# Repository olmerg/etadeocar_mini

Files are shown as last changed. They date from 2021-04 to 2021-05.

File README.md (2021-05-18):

# Tadeo Car
## Robótica industrial
Con este proyecto se busca diseñar a escala el vehículo eléctrico proyecto ETadeo Car, realizado por la universidad de Bogotá Jorge Tadeo Lozano. Este vehículo corresponde a un modelo eléctrico con tracción de cuatro ruedas utilizando servomotores [Dynamixel](http://www.dynamixel.com). El desarrollo incluye las etapas de; diseño, construcción, prueba de motores, construcción del circuito teniendo en cuenta la posibilidad de control mediante bluetooth y programación del controlador integrando la cinemática del robot para relacionarlo con velocidad lineal y angular de entrada.

El resultado final de este proyecto se encuentra en [este enlace](https://youtu.be/BBhkFSA11gs).

## Industrial robotics 2021-1
This project seeks to scale the electric vehicle ETadeo Car project, carried out by the University of Bogotá Jorge Tadeo Lozano. This vehicle corresponds to an electric model with four-wheel drive using [Dynamixel](http://www.dynamixel.com) servo motors. Development includes the stages of; design, construction, motor testing, circuit construction taking into account the possibility of bluetooth control and controller programming integrating the kinematics of the robot to relate it to linear and angular input velocity.

The final result of this project can be found at [this link](https://youtu.be/BBhkFSA11gs).

### Construccción
Teniendo en cuenta el diseño determinado para lograr una escala aproximada en la estructura de 1:4, son empleados elementos de la marca robotis para la construcción de cada una de los grupos móviles de joint y wheel.
Como elemento chasis se tiene el uso de riel DIN, con el fin de lograr una estructura rígida, reduciendo el peso y con ventajas para el ensamble rápido y ajustes ante cambios que puedan presentarse en el diseño.  Es importante tener en cuenta el acople entre cables para lograr la extensión que permita alcanzar la distancia parámetro entre la base de las ruedas. Sin embargo, es fundamental observar la forma de entrada en los motores, ya que estos no permiten adaptabilidad a modelos que se puedan encontrar en el mercado genérico. Esto lo convierte en un recurso limitante en la construcción del modelo a escala junto con los tornillos que permiten la unión de las partes.

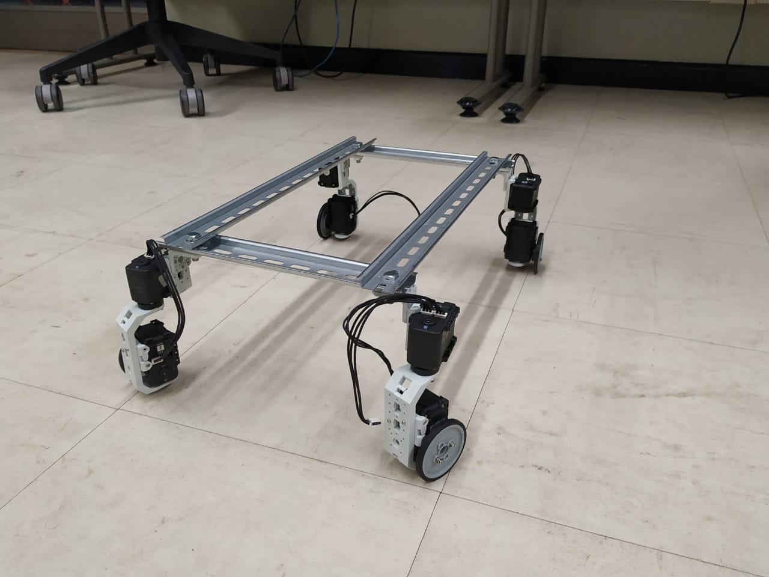
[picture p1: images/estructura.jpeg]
Estructura eTadeoCar


Antes de hacer la unión de los grupos de joint y wheel al chasis, se realizaron pruebas con los motores en el software Dynamixel Wizard 2.0 con la utilización de el hardware de robotis USB2Dynamixel, quien precisa de un controlador en el computador para su uso efectivo. En este se caracterizaron los motores según el movimiento que realizan (joint o wheel), se configuraron las ID para utilizar en la programación y los baudios de comunicación, los cuales son adaptados en 1000000.

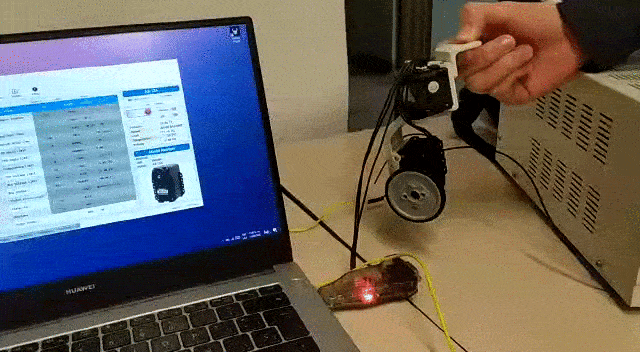
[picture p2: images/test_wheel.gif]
Dynamixel wheel

Dynamixel joint

### URDF
Se modeló el robot utilzando URDF dentro del entorno de ROS, utilizando piezas generadas en formato .stl en el programa Autodesk Inventor. Este modelo sirvio para observar la posición y los movimientos que podía tener cada joint y cada wheel.
(Las piezas pueden ser encontradas [aquí](Piezas)).

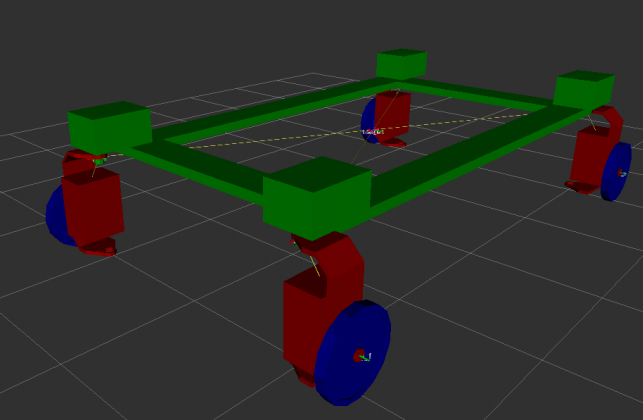
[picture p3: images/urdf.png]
urdf


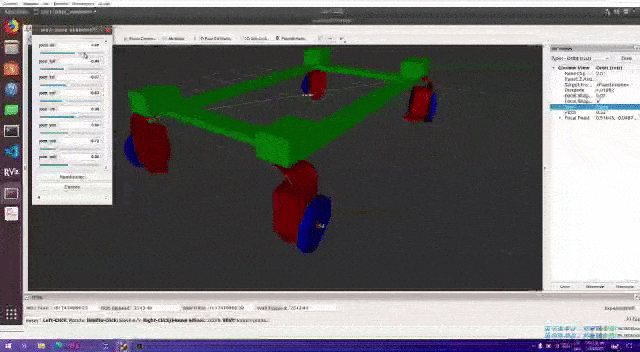
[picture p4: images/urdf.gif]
urdf


Del cual se generó la cadena cinemática

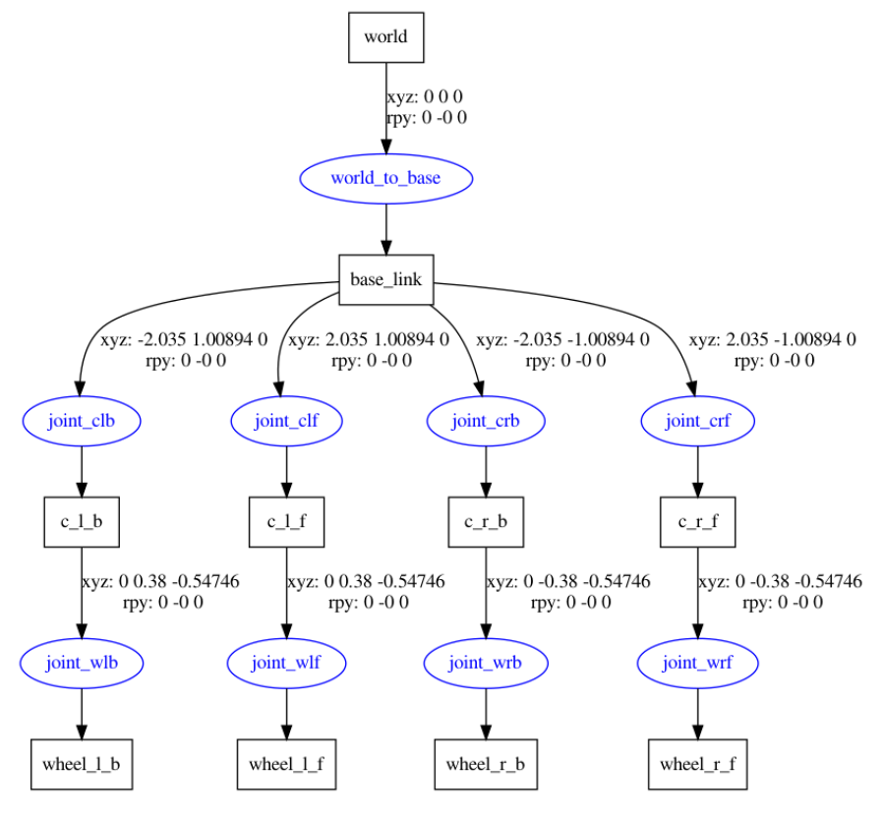
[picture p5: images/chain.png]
kinematic chain


### Circuito
Los componentes inmersos en el circuito que permite el funcionamiento del modelo son; controlador Arduino Mega 2560. Integrado SN74lS241N, el cual permite la comunicación entre el controlador y los motores al ser un buffer tri-estado. Módulo bluetooth HC-06 para el control remoto del modelo a escala. Fuente de poder que permita la alimentación de los motores dynamixel. (FotoCircuito)

El funcionamiento de este circuito puede describirse desde la potencia de entrada, para esto fue empleada la fuente que nos permite tener a la salida 12V a 5A DC, siendo adecuada para la alimentación de los motores dynamixel. Es importante destacar el negativo común para el controlador y el integrado. Adicional a esto, se debe tener en cuenta el orden de los pines para iniciar la serie que alimenta los motores 

Dynamixel pinout

La conexión del circuito integrado nos permite tener la comunicación entre el controlador Arduino Mega 2560 y los motores Dynamixel, debido a el tratamiento que este le da a los datos para permitir figurar como transmisor y receptor. En el caso descrito se utiliza el pin 2 de Arduino como pin de control y los pines 18 y 19, correspondientes a TX1 y RX1 correspondientemente. Se deben tener en cuenta conexiones propias del circuito para su funcionamiento Para el funcionamiento del módulo bluetooth realizamos la conexión de TXD del HC-06 al pin 15 de la placa Arduino correspondiente al RX3. Por su parte, el Pin RXD está conectado al pin 14 de la placa Arduino correspondiente a TX3.
El voltaje positivo de 5v para la alimentación de la placa Arduino se obtiene de la fuente brindada por el computador. La alimentación del circuito integrado y el módulo bluetooth es obtenido de la fuente del Arduino, utilizando su salida de 5v. No olvidar que es común el valor correspondiente a  0V. Se encuentra contenido en el repositorio el circuito impreso.

Las conexiones en protoboard del circuito se presentan a continuación junto con el diseño realizado en Proteus.

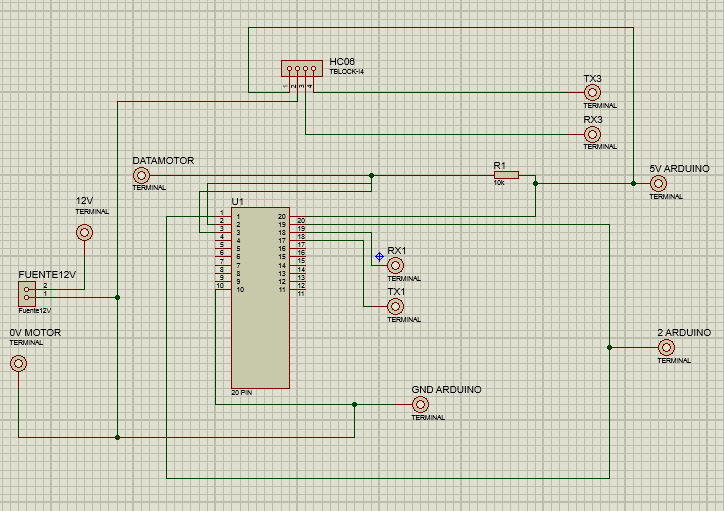
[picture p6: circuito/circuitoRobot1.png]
Proteus Circuit

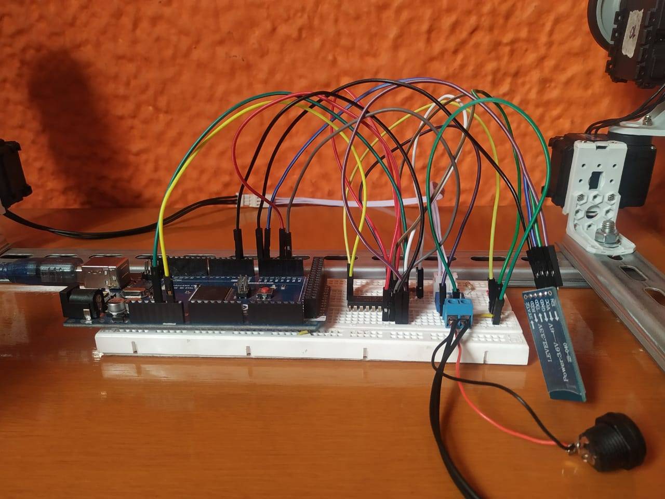
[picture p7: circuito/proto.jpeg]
Protoboard


### Código

Se programaron los servomotores utilizando [Arduino](https://www.arduino.cc) con la librería `Dynamixel.h`, las funciones creadas para desarrollar toda la lógica de funcionamiento fueron:

```
/**
 * Calcula la velocidad que debe tener cada rueda
*/
void computeVel()
```
```
/**
 * Calculan el ángulo de cada joint
*/
void computeAng()
void computeAngAux()
```
```
/**
 * Retorna el sentido de giro de la rueda
 * Toma de parámetro la velocidad
*/
int selectSide(float vel)
```
```
/**
 * Pone en movimiento cada una de las ruedas
*/
void runCar()
```
```
/**
 * Gira cada joint a la posición deseada
*/
void turn()
```
```
/**
 * Deja los joint en posiciión 0
 * Detiene todos los motores
*/
void stopAll()
```
### Conexión Bluetooth

Con el uso de la aplicación bluetooth electronics descargada en Android, se permite la realización de un panel para control del modelo. Esta aplicación se conecta de forma sencilla con el módulo para iniciar la transmisión de datos.
Como se aprecia en la imágen, se utiliza un pad de 4 posiciones para enviar el carácter deseado que se procesa en el código para su ejecución en los motores Dynamixel. También se cuenta con un botón de parada, útil en cualquier momento ante algún imprevisto que se pueda presentar durante la ejecución. 

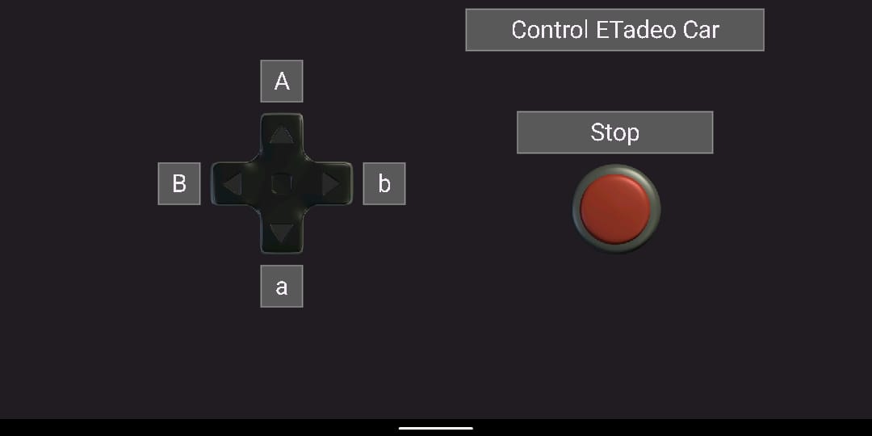
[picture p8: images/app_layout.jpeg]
Bluetooth App


En esta aplicación se emplea un pad de 4 posiciones para enviar un caracter que esta relacionado con el código en la programación, asociado respectivamente con un movimiento específico. En este caso como se aprecia en la imágen, los caracteres utilizados para el movimiento del robot son A, a, B, b. Por su parte, se emplea un botón (buttons) de color rojo, el cual está asociado al caracter s para el paro del robot y vuelta a la posición inicial. La aplicacion se encuentra en [esta ruta](App).

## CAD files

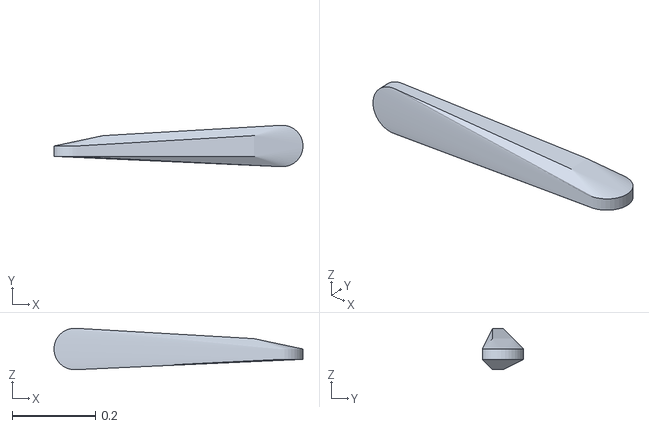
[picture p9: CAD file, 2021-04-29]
lesson_urdf/meshes/collision/arm_link_twist_2.stl
0.6 x 0.0997 x 0.0997

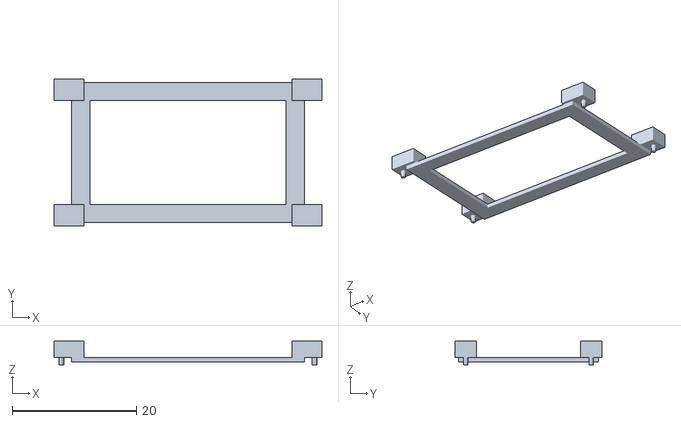
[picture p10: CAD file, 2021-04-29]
Piezas/Rieles.stl
43.1 x 23.7 x 3.80

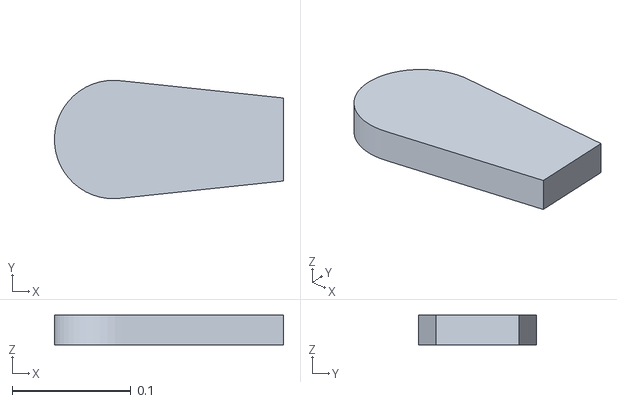
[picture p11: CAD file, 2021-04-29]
lesson_urdf/meshes/collision/gripper.stl
0.193 x 0.1 x 0.025

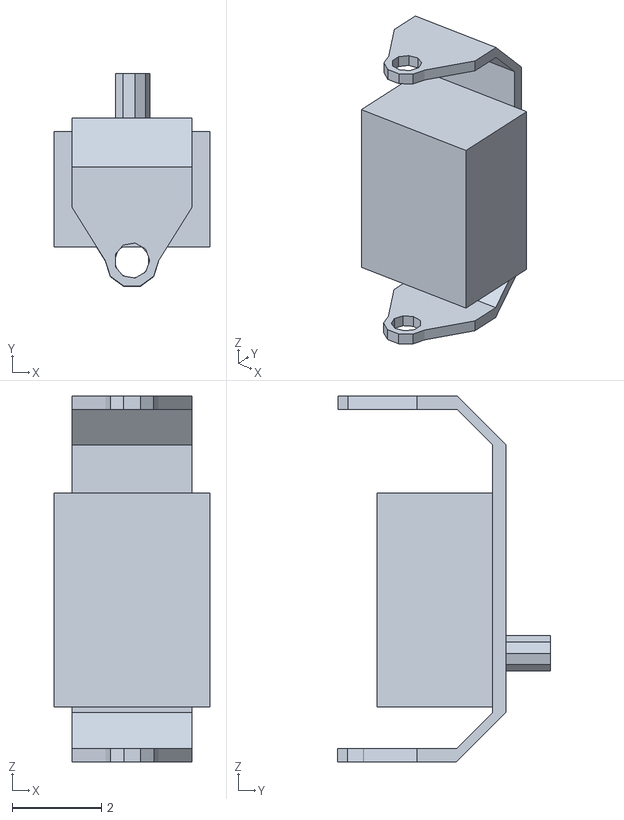
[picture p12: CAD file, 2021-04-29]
Piezas/C_motor.stl
3.50 x 4.79 x 8.21

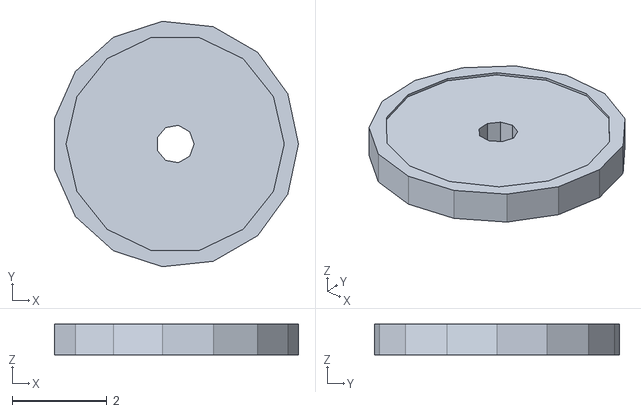
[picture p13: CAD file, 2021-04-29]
Piezas/Rueda.stl
5.14 x 5.17 x 0.65

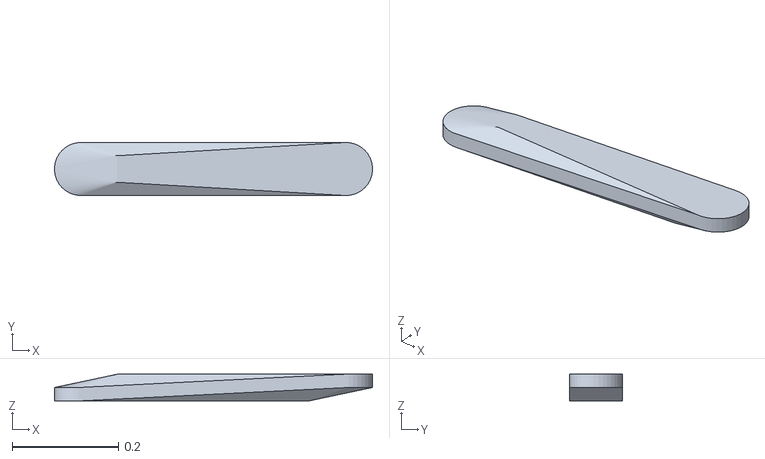
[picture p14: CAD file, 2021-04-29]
lesson_urdf/meshes/collision/arm_link.stl
0.6 x 0.0997 x 0.05

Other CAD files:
lesson_urdf/meshes/collision/arm_link_twist_1.stl
Piezas/C_motor.ipt
Piezas/Rieles.ipt
Piezas/Rueda.ipt

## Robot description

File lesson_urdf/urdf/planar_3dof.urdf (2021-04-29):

<?xml version="1.0"?>

<robot name="mobile">

    <material name="red">
        <color rgba="0.6 0.0 0.0 2"/>
    </material>

    <material name="green">
        <color rgba="0 0.6 0 2"/>
    </material>

    <material name="blue">
        <color rgba="0 0 0.6 2"/>
    </material>

	<link name="world" />

    <link name="base_link">
        <visual>
            <geometry>
                <mesh filename="package://lesson_urdf/meshes/visual/rieles.stl" scale="0.1 0.1 0.1"/>
            </geometry>
            <material name="green"/>
        </visual>
    </link>

    <joint name="world_to_base" type="fixed">
        <parent link="world"/>
        <child link="base_link"/>
    </joint>

    <!--LEG_L_F-->

    <link name="c_l_f">
        <visual>
            <geometry>
                <mesh filename="package://lesson_urdf/meshes/visual/c.stl" scale="0.1 0.1 0.1"/>
            </geometry>
            <material name="red"/>
        </visual>
    </link>

    <joint name="joint_clf" type="revolute">
        <parent link="base_link"/>
        <child link="c_l_f"/>
        <origin xyz="2.035 1.00894 0.0"/>
        <axis xyz="0.0 0.0 1.0"/>
        <limit lower="-1.57" upper="1.57" effort="0.5" velocity="0.5"/>
    </joint>

    <link name="wheel_l_f">
        <visual name="">
            <origin xyz="0.0 0.0 0.0" rpy="1.57 0.0 0.0"/>
            <geometry>
                <mesh filename="package://lesson_urdf/meshes/visual/rueda.stl" scale="0.1 0.1 0.1"/>
            </geometry>
            <material name="blue"/>
        </visual>
    </link>

    <joint name="joint_wlf" type="continuous">
        <origin xyz="0.0 0.38 -0.54746" rpy="0.0 0.0 0.0"/>
        <parent link="c_l_f"/>
        <child link="wheel_l_f"/>
        <axis xyz="0.0 1.0 0.0"/>
    </joint>

    <!--LEG_R_F-->

     <link name="c_r_f">
        <visual>
            <origin rpy="0 0 3.14159" xyz="0 0 0"/>
            <geometry>
                <mesh filename="package://lesson_urdf/meshes/visual/c.stl" scale="0.1 0.1 0.1"/>
            </geometry>
            <material name="red"/>
        </visual>
    </link>

    <joint name="joint_crf" type="revolute">
        <parent link="base_link"/>
        <child link="c_r_f"/>
        <origin xyz="2.035 -1.00894 0.0"/>
        <axis xyz="0.0 0.0 1.0"/>
        <limit lower="-1.57" upper="1.57" effort="0.5" velocity="0.5"/>
    </joint>

    <link name="wheel_r_f">
        <visual name="">
            <origin xyz="0.0 0.0 0.0" rpy="1.57 0.0 0.0"/>
            <geometry>
                <mesh filename="package://lesson_urdf/meshes/visual/rueda.stl" scale="0.1 0.1 0.1"/>
            </geometry>
            <material name="blue"/>
        </visual>
    </link>

    <joint name="joint_wrf" type="continuous">
        <origin xyz="0.0 -0.38 -0.54746" rpy="0.0 0.0 0.0"/>
        <parent link="c_r_f"/>
        <child link="wheel_r_f"/>
        <axis xyz="0.0 1.0 0.0"/>
    </joint>

    <!--LEG_L_B-->

    <link name="c_l_b">
        <visual>
            <geometry>
                <mesh filename="package://lesson_urdf/meshes/visual/c.stl" scale="0.1 0.1 0.1"/>
            </geometry>
            <material name="red"/>
        </visual>
    </link>

    <joint name="joint_clb" type="revolute">
        <parent link="base_link"/>
        <child link="c_l_b"/>
        <origin xyz="-2.035 1.00894 0.0"/>
        <axis xyz="0.0 0.0 1.0"/>
        <limit lower="-1.57" upper="1.57" effort="0.5" velocity="0.5"/>
    </joint>

    <link name="wheel_l_b">
        <visual name="">
            <origin xyz="0.0 0.0 0.0" rpy="1.57 0.0 0.0"/>
            <geometry>
                <mesh filename="package://lesson_urdf/meshes/visual/rueda.stl" scale="0.1 0.1 0.1"/>
            </geometry>
            <material name="blue"/>
        </visual>
    </link>

    <joint name="joint_wlb" type="continuous">
        <origin xyz="0.0 0.38 -0.54746" rpy="0.0 0.0 0.0"/>
        <parent link="c_l_b"/>
        <child link="wheel_l_b"/>
        <axis xyz="0.0 1.0 0.0"/>
    </joint>

    <!--LEG_R_B-->

    <link name="c_r_b">
        <visual>
            <origin rpy="0 0 3.14159" xyz="0 0 0"/>
            <geometry>
                <mesh filename="package://lesson_urdf/meshes/visual/c.stl" scale="0.1 0.1 0.1"/>
            </geometry>
            <material name="red"/>
        </visual>
    </link>

    <joint name="joint_crb" type="revolute">
        <parent link="base_link"/>
        <child link="c_r_b"/>
        <origin xyz="-2.035 -1.00894 0.0"/>
        <axis xyz="0.0 0.0 1.0"/>
        <limit lower="-1.57" upper="1.57" effort="0.5" velocity="0.5"/>
    </joint>

    <link name="wheel_r_b">
        <visual name="">
            <origin xyz="0.0 0.0 0.0" rpy="1.57 0.0 0.0"/>
            <geometry>
                <mesh filename="package://lesson_urdf/meshes/visual/rueda.stl" scale="0.1 0.1 0.1"/>
            </geometry>
            <material name="blue"/>
        </visual>
    </link>

    <joint name="joint_wrb" type="continuous">
        <origin xyz="0.0 -0.38 -0.54746" rpy="0.0 0.0 0.0"/>
        <parent link="c_r_b"/>
        <child link="wheel_r_b"/>
        <axis xyz="0.0 1.0 0.0"/>
    </joint>



</robot>

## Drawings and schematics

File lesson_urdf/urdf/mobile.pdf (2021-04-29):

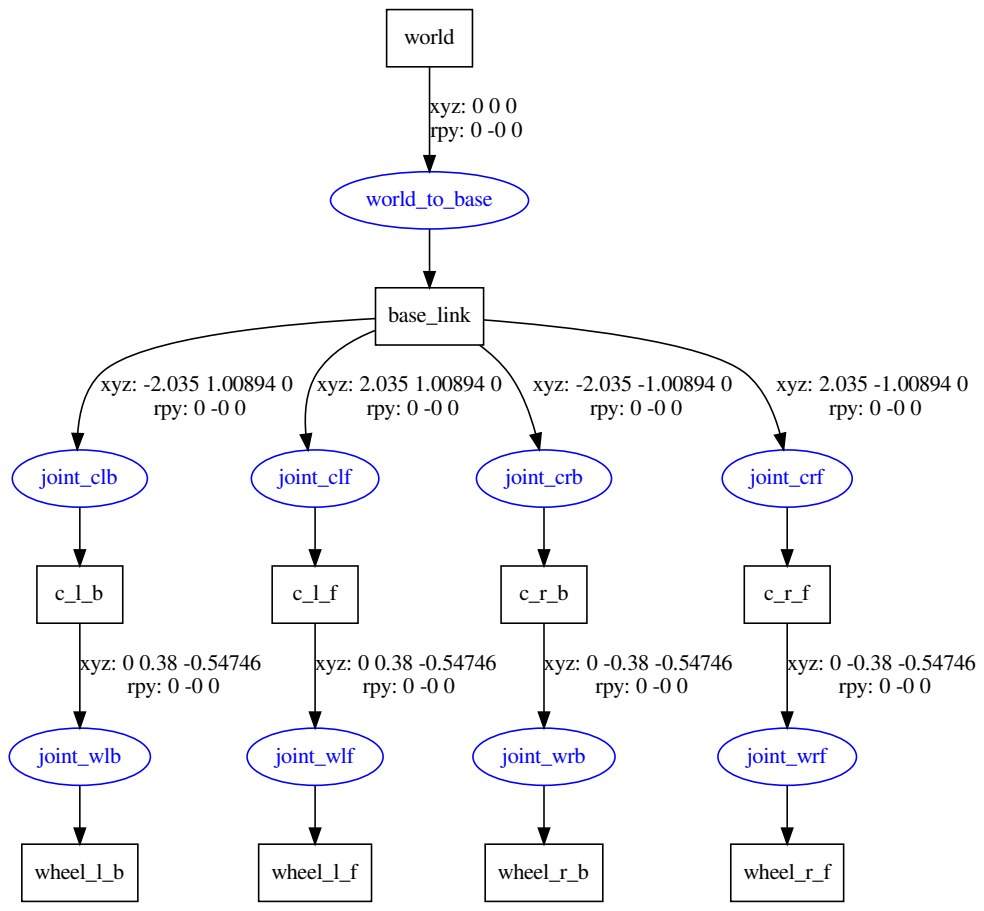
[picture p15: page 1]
world; world_to_base; xyz: 0 0 0 rpy: 0 -0 0; base_link; joint_clb; xyz: -2.035 1.00894 0 rpy: 0 -0 0; joint_clf; xyz: 2.035 1.00894 0 rpy: 0 -0 0; joint_crb; xyz: -2.035 -1.00894 0 rpy: 0 -0 0; joint_crf; xyz: 2.035 -1.00894 0 rpy: 0 -0 0; joint_wlb; xyz: 0 0.38 -0.54746 rpy: 0 -0 0; wheel_l_b; joint_wlf; wheel_l_f; joint_wrb; xyz: 0 -0.38 -0.54746 rpy: 0 -0 0; wheel_r_b; joint_wrf; wheel_r_f

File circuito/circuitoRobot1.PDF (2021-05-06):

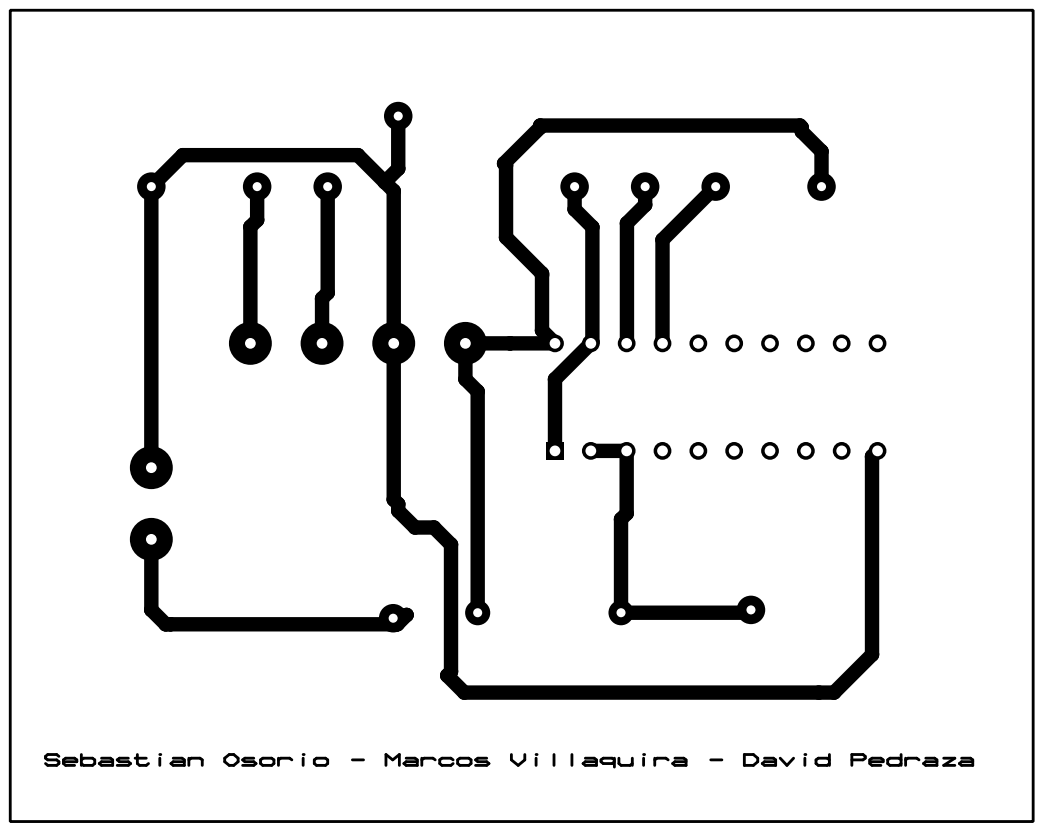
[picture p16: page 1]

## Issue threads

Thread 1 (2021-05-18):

URDF is in inches

olmerg, 2021-05-18:
El urdf se encuentra el pulgadas, por lo cual como primera medida se deben subir los archivos realizados en inventor y ojala la exportación de los stl correctamente.

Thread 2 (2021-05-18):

subir archivo del panel del app

olmerg, 2021-05-18:
En el app de android se puede descargar el panel y subirlo aqui, junto con una explicación en el readme

SebastianOsoriop, 2021-05-18:
En la carpeta App se encuentra el archivo ETadeo_Car_PanelBluetooth.kwl, el cuál corresponde al panel de la aplicación Bluetooth electronics. Además se actualizó el readme para mostrar la parte del código que hace referencia a los caracteres (B, b, A, a ) del panel y descripción de la elaboración del panel en la aplicación

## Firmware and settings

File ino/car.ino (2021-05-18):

#include <DynamixelSerial.h>
#define M_PI 3.14159265358979323846
#define M_PI_2 1.57079632679489661923

int CAMBIO_VEL_LIN = 30;
int CAMBIO_VEL_ANG = 3;
int OFFSET_L_FRONT = 650;
int OFFSET_R_FRONT = 0; //encontrar experimentalmente
int OFFSET_L_REAR = 450;
int OFFSET_R_REAR = 0; //encontrar experimentalmente

/**
 * Definición de los motores de dirección
*/
int dir_left_front = 11;
int dir_right_front = 17;
int dir_left_rear = 13;
int dir_right_rear = 14;

/**
 * Definición de los motores de las ruedas
*/
int wheel_left_front = 1;
int wheel_right_front = 2;
int wheel_left_rear = 10;
int wheel_right_rear = 3;

/**
 * Velocidades angular y lineal deseadas
*/
float ang_vel_des = 0;
float lin_vel_des = 0;
/**
 * Velocidad que debe tomar cada motor de rueda
*/
float vel_left_front = 0;
float vel_right_front = 0;
float vel_left_rear = 0;
float vel_right_rear = 0;

/**
 * Velocidad que debe tomar cada motor de dirección
*/
float front_left_steering = 0;
float front_right_steering = 0;
float rear_left_steering = 0;
float rear_right_steering = 0;

/**
 * Medidas tomadas del vehículo
*/
double track_ = 27;
double radius_ = 3;
double base_ = 10;

void setup()
{
    Dynamixel.setSerial(&Serial1);
    Dynamixel.begin(1000000, 2);
    Serial.begin(115200);
    Serial3.begin(9600);
    delay(1000);
}
/**
 * Calcula la velocidad que debe tener cada rueda
*/
void computeVel()
{
    vel_left_front = copysign(1.0, lin_vel_des) * sqrt((pow(lin_vel_des - ang_vel_des * track_ / 2, 2) + pow(base_ * ang_vel_des / 2.0, 2))) / radius_;
    vel_right_front = copysign(1.0, lin_vel_des) * sqrt((pow(lin_vel_des + ang_vel_des * track_ / 2, 2) + pow(base_ * ang_vel_des / 2.0, 2))) / radius_;
    vel_left_rear = copysign(1.0, lin_vel_des) * sqrt((pow(lin_vel_des - ang_vel_des * track_ / 2, 2) + pow(base_ * ang_vel_des / 2.0, 2))) / radius_;
    vel_right_rear = copysign(1.0, lin_vel_des) * sqrt((pow(lin_vel_des + ang_vel_des * track_ / 2, 2) + pow(base_ * ang_vel_des / 2.0, 2))) / radius_;
}

/**
 * Calcula el ángulo de cada joint
*/
void computeAng()
{
    front_left_steering = atan2(ang_vel_des * base_, (2.0 * lin_vel_des - ang_vel_des * track_));
    front_right_steering = atan2(ang_vel_des * base_, (2.0 * lin_vel_des + ang_vel_des * track_));
    rear_left_steering = -atan2(ang_vel_des * base_, (2.0 * lin_vel_des - ang_vel_des * track_));
    rear_right_steering = -atan2(ang_vel_des * base_, (2.0 * lin_vel_des + ang_vel_des * track_));
}

/**
 * Calculan el ángulo de cada joint
*/
void computeAngAux()
{
    front_left_steering = copysign(M_PI_2, ang_vel_des);
    front_right_steering = copysign(M_PI_2, ang_vel_des);
    rear_left_steering = copysign(M_PI_2, -ang_vel_des);
    rear_right_steering = copysign(M_PI_2, -ang_vel_des);
}

/**
 * Retorna el sentido de giro de la rueda
 * Toma de parámetro la velocidad
*/
int selectSide(float vel)
{
    return vel < 0;
}

/**
 * Pone en movimiento cada una de las ruedas
*/
void runCar()
{
    Dynamixel.setEndless(wheel_left_front, ON);
    Dynamixel.setEndless(wheel_right_front, ON);
    Dynamixel.setEndless(wheel_left_rear, ON);
    Dynamixel.setEndless(wheel_right_rear, ON);

    int temp_vel_1 = map(abs(vel_left_front), 0, 50, 0, 1023);
    int temp_vel_2 = map(abs(vel_right_front), 0, 50, 0, 1023);
    int temp_vel_3 = map(abs(vel_left_rear), 0, 50, 0, 1023);
    int temp_vel_4 = map(abs(vel_right_rear), 0, 50, 0, 1023);

    Dynamixel.turn(wheel_left_front, selectSide(vel_left_front), temp_vel_1);
    Dynamixel.turn(wheel_right_front, selectSide(vel_right_front), temp_vel_2);
    Dynamixel.turn(wheel_left_rear, selectSide(vel_left_rear), temp_vel_3);
    Dynamixel.turn(wheel_right_rear, selectSide(vel_right_rear), temp_vel_4);

}

/**
 * Gira cada joint a la posición deseada
*/
void turn(){

    int temp_ang_1 = map(front_left_steering * RAD_TO_DEG, -90, 90, 0, 306);
    int temp_ang_2 = map(front_right_steering * RAD_TO_DEG, -90, 90, 0, 306);
    int temp_ang_3 = map(rear_left_steering * RAD_TO_DEG, -90, 90, 0, 306);
    int temp_ang_4 = map(rear_right_steering * RAD_TO_DEG, -90, 90, 0, 306);

    if (front_left_steering  < 0) temp_ang_1 *= -1;
    if (front_right_steering < 0) temp_ang_2 *= -1;
    if (rear_left_steering   < 0) temp_ang_3 *= -1;
    if (rear_right_steering  < 0) temp_ang_4 *= -1;

    /*
    *Comentar esta líne para hacer pruebas del sentido de giro*
    */
    Dynamixel.move(dir_left_front, temp_ang_1 + OFFSET_L_FRONT - 153); 
    Dynamixel.move(dir_right_front, temp_ang_2 + OFFSET_R_FRONT - 153); 
    Dynamixel.move(dir_left_rear, temp_ang_3 + OFFSET_L_REAR - 153); 
    Dynamixel.move(dir_right_rear, temp_ang_4 + OFFSET_R_REAR - 153); 
    
    /*
    *Para observar mejor en las peruabs de sentido de giro*
    */
    // Dynamixel.move(dir_left_front, 0);
    // Dynamixel.move(dir_right_front, 0);
    // Dynamixel.move(dir_left_rear, 1023);
    // Dynamixel.move(dir_right_rear, 0);

}


/**
 * Deja los joint en posiciión 0
 * Detiene todos los motores
*/
void stopAll()
{
    Dynamixel.setEndless(wheel_left_front, OFF);
    Dynamixel.setEndless(wheel_right_front, OFF);
    Dynamixel.setEndless(wheel_left_rear, OFF);
    Dynamixel.setEndless(wheel_right_rear, OFF);

    Dynamixel.move(dir_left_front, OFFSET_L_FRONT);
    Dynamixel.move(dir_right_front, OFFSET_R_FRONT);
    Dynamixel.move(dir_left_rear, OFFSET_L_REAR);
    Dynamixel.move(dir_right_rear, OFFSET_R_REAR);
    Dynamixel.move(wheel_left_front, 0); 
    Dynamixel.move(wheel_right_front, 0);
    Dynamixel.move(wheel_left_rear, 0);
    Dynamixel.move(wheel_right_rear, 0);
}

void loop()
{
    unsigned char comando = 0;
    if (Serial.available())
    {
        comando = Serial.read();
        if (comando == 'a')
            lin_vel_des += CAMBIO_VEL_LIN;
        else if (comando == 'A')
            lin_vel_des -= CAMBIO_VEL_LIN;
        else if (comando == 'b')
            ang_vel_des += CAMBIO_VEL_ANG;
        else if (comando == 'B')
            ang_vel_des -= CAMBIO_VEL_ANG;
        else if (comando == 's' || comando == 'S')
        {
            lin_vel_des = 0;
            ang_vel_des = 0;
        }
    }

    if (abs(2 * lin_vel_des) > abs(ang_vel_des * track_))
    {
        computeVel();
        runCar();
    }
    if (abs(2 * lin_vel_des) > abs(ang_vel_des * track_))
    {
        computeAng();
        turn();
    }
    else if (abs(lin_vel_des) > 0.001)
    {
        computeAngAux();
        turn();
    }
    else if (lin_vel_des == 0 && ang_vel_des == 0) stopAll();
    delay(500);
}

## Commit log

2021-04-29 primer commit
    [arm_link.stl, arm_link_twist_1.stl, arm_link_twist_2.stl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]
2021-05-06 Añadidas las imagenes, circuito e info en el readme
2021-05-18 añadidas las piezas
    [C_motor.ipt, C_motor.stl, Rieles.ipt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]
